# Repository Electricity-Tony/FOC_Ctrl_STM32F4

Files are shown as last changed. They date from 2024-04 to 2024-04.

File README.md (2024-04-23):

# FOC_Ctrl_STM32F4

* 基于 stm32F405rgt6 开发的 FOC 中大功率开发板

## 1 PCB设计文件

* stm32F405RGT6 minisystem

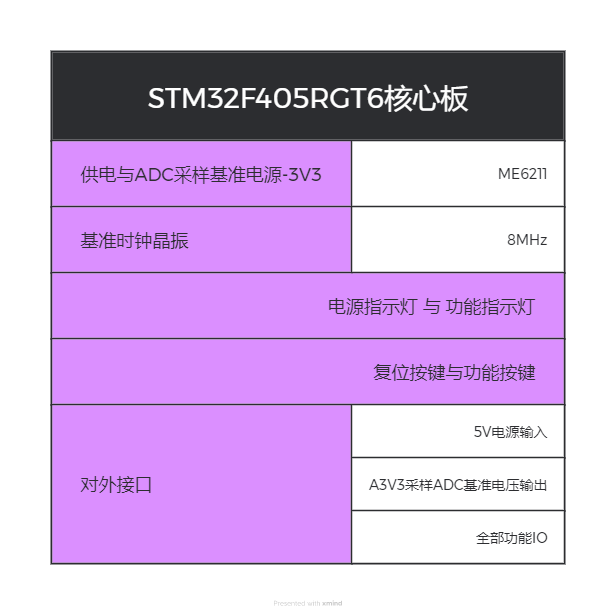
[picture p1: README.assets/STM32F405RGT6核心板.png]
STM32F405RGT6核心板


* power_board

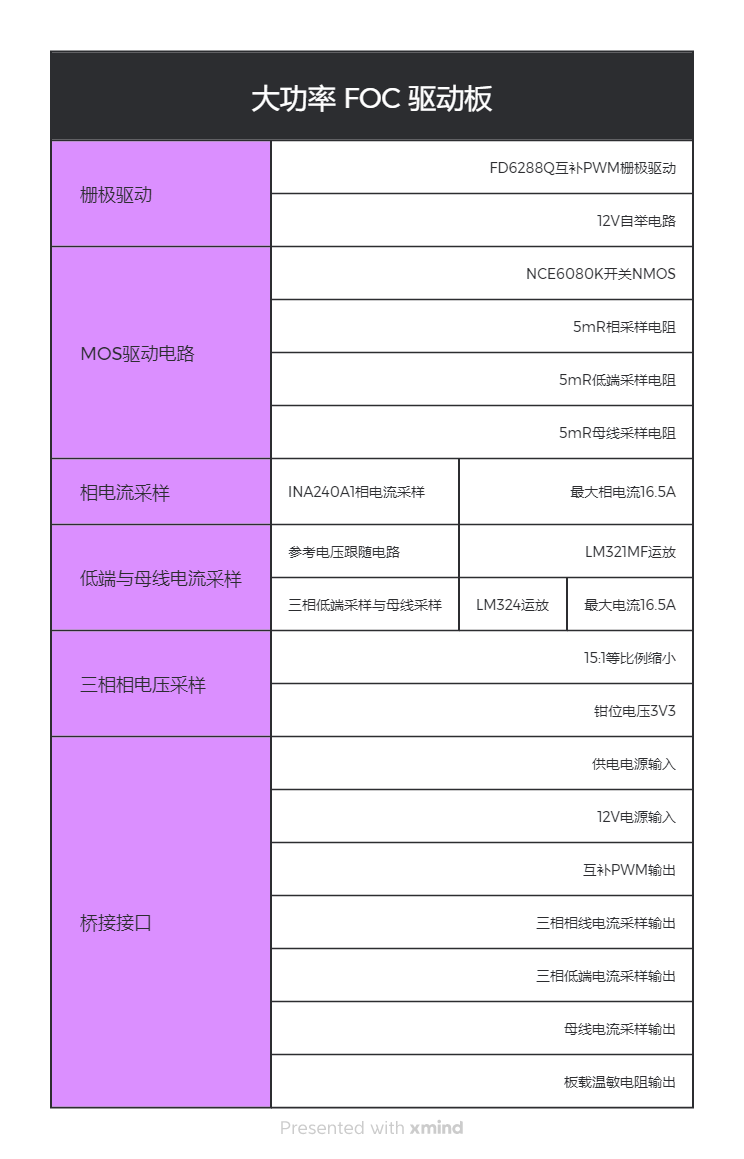
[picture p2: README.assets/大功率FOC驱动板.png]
大功率 FOC 驱动板


* base_board

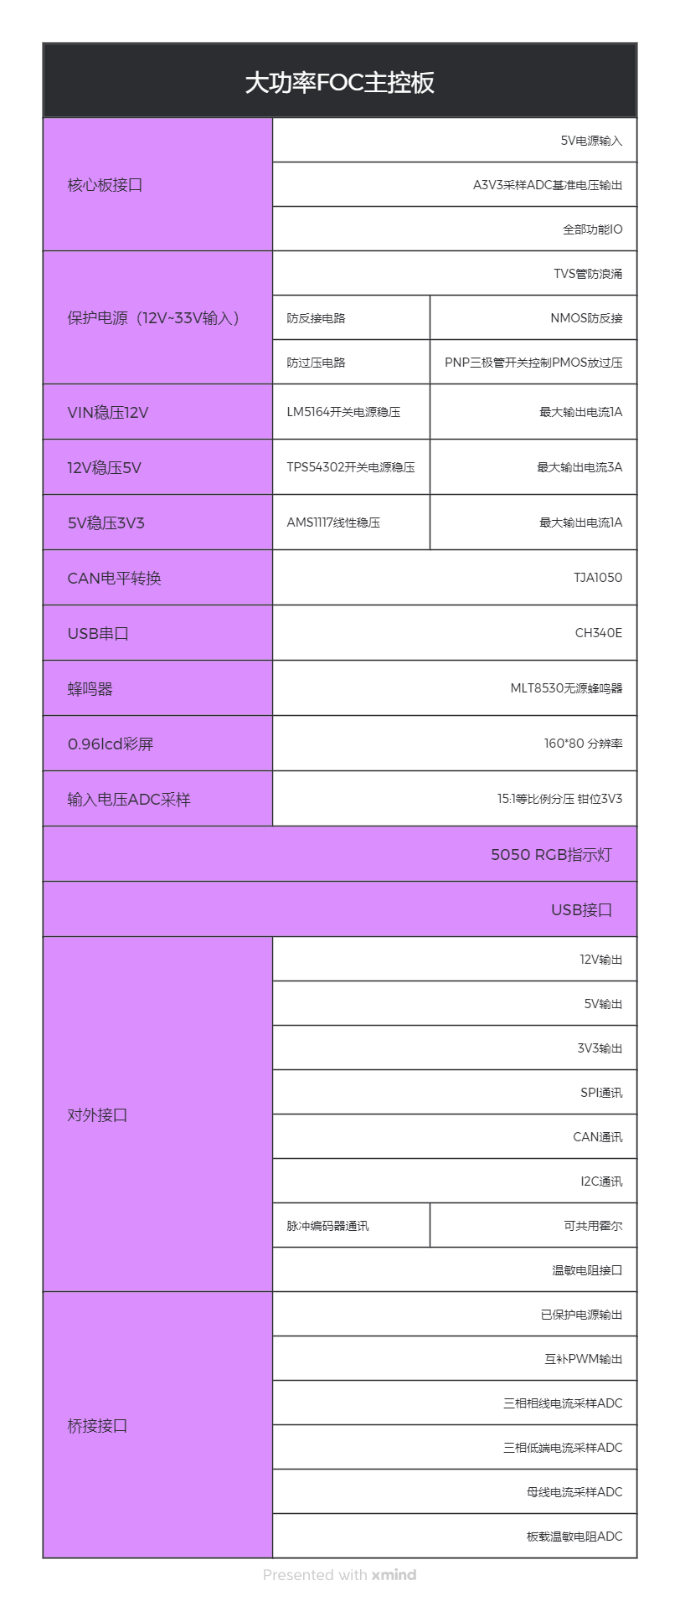
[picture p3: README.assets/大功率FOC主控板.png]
大功率FOC主控板


### 1 控制板设计文件

#### 1.1 输入电路设计

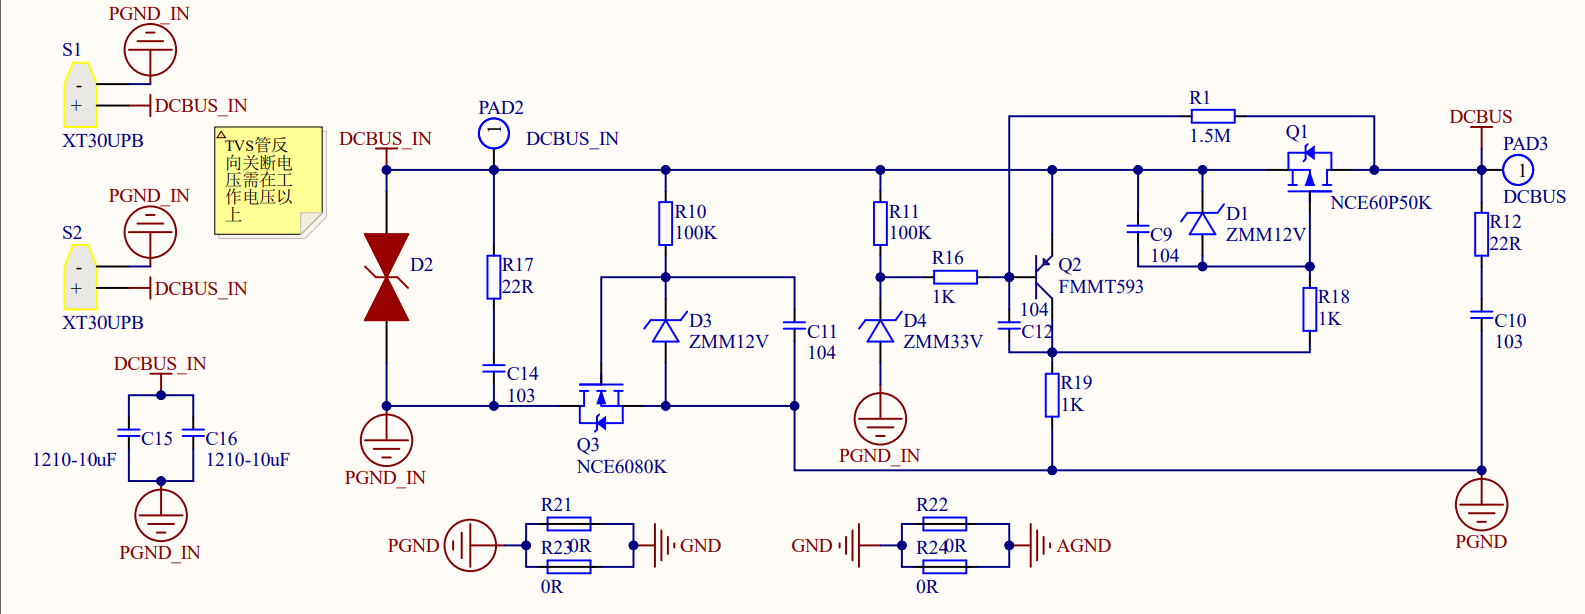
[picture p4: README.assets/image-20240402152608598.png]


* NCE6080K nmos 实现电源防反接
* NCE60P50K pmos 通过三极管及稳压管实现防过压
* RC 电路实现环启动
* TVS 管浪涌保护

> 实测反接保护与过压保护均可实现

#### 1.2 稳压电路设计

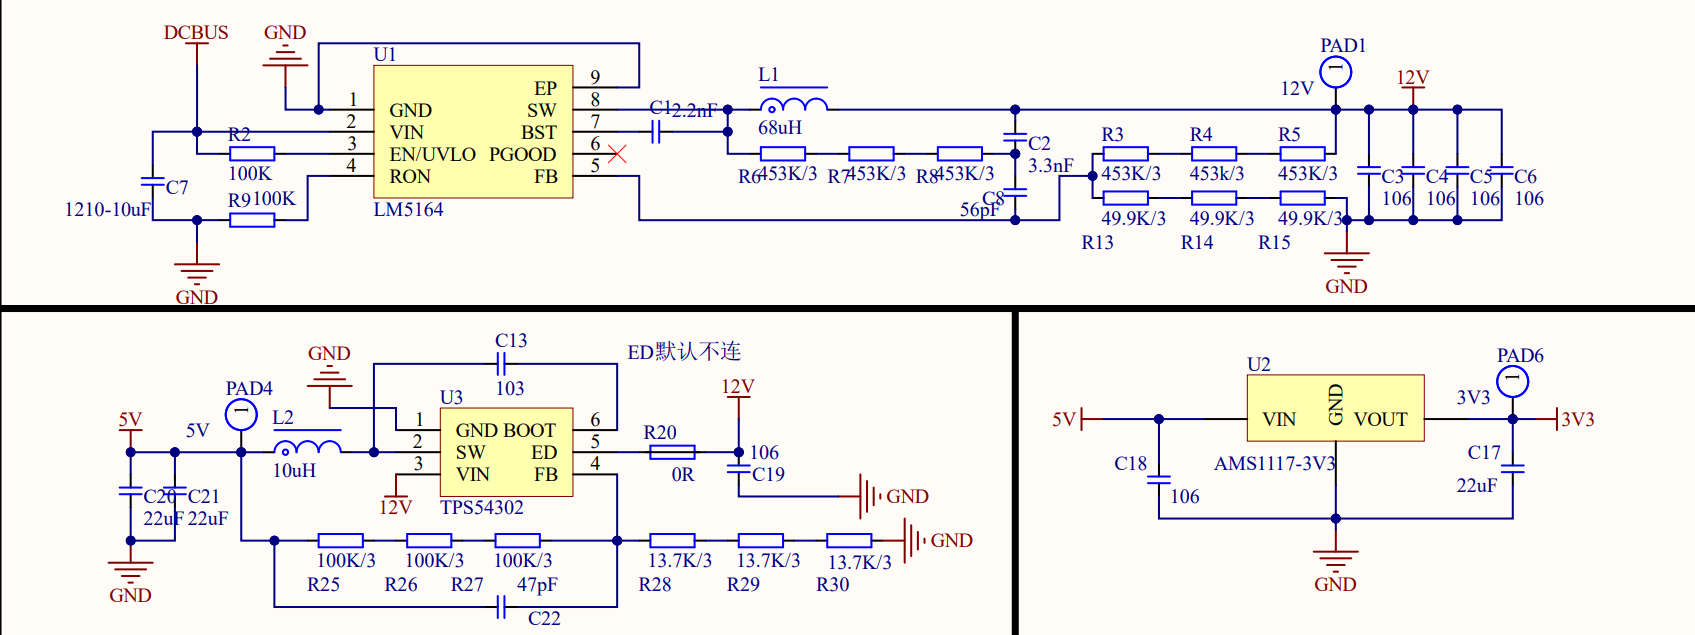
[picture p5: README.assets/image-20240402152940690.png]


* LM5164 宽幅电压输入 ，稳压12V，最大电流1A
* TP54302 稳压5V
* AMS1117 LDO稳压3V3

> LM5164 中 C1 = 2.2nF  必须要焊接，才能正常输出，3.3nF与56pF用于减少输出纹波，具体选择大小见datasheet
>
> 输出电压计算：$R_{FB2} = \frac{1.2V}{V_{OUT}-1.2V} \cdot R_{FB1}$
>
> 其余参数详见 datasheet

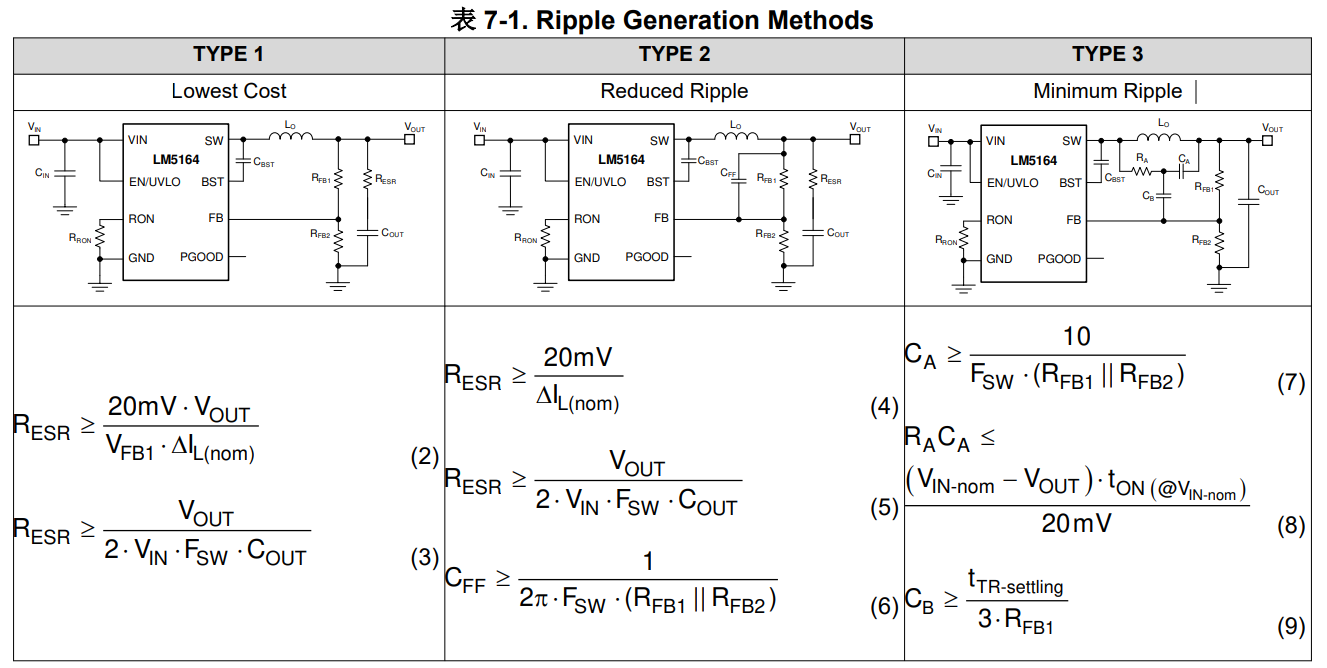
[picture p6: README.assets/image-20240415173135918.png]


> TPS54302 ED 角位欠压锁定角，内部上拉，当ED电压低于阈值电压实现欠压锁定，一般而言悬空即可使用，不使用欠压锁定功能
>
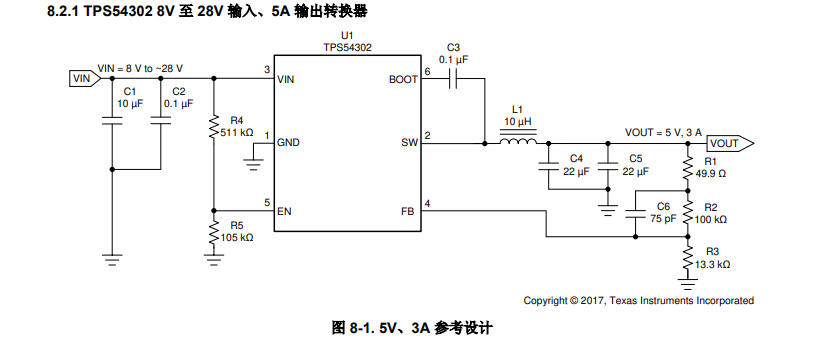
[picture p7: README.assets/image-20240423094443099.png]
> 
>
> 
>
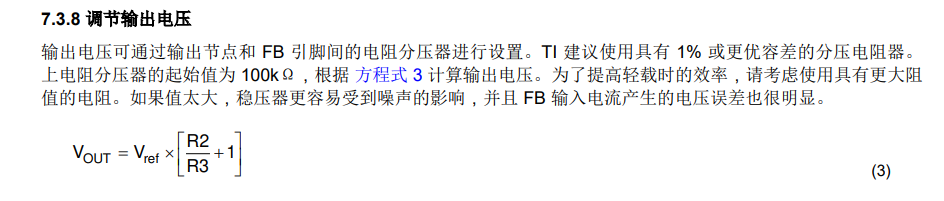
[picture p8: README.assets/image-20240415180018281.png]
> 输出电压计算：
>
> $V_{ref} = 0.596V$ , R2为分压上电阻，R3为分压下电阻

#### 1.3 外设设计

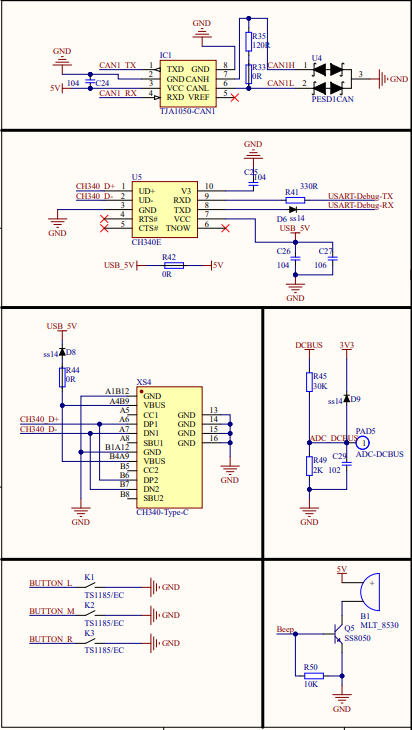
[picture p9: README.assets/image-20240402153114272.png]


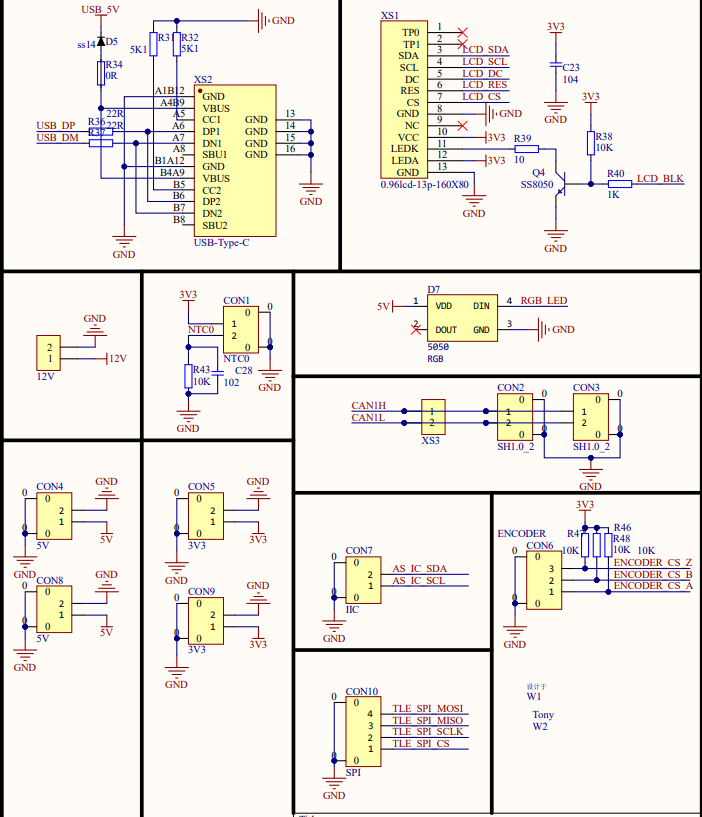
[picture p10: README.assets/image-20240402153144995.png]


* 预留外设 CAN，USART，USB，蜂鸣器，LCD屏幕，3个独立按键，各编码器通讯及供电接口

> CAN 中断电阻可通过是否焊接或短接 0R 电阻焊盘实现
>
> 5V 网络 与 USB5V 网络可通过 0R电阻 选择是否隔离，USB5V只提供给CH340串口芯片，避免主控反复上下电需要重新选择串口
>
> 串口 USB 的5V输入串接了一个二极管，纯在 0.7V 左右的压降，根据需要选择是否焊接

### 2 驱动板设计文件

#### 2.1 栅极驱动与自举电路

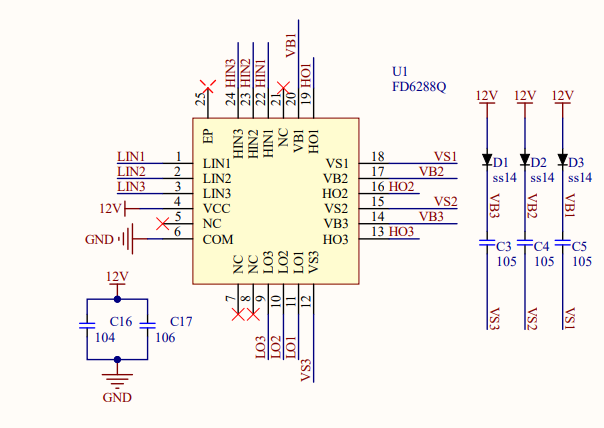
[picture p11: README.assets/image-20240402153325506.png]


* FD6288Q 栅极驱动，自带50ns死区保护，自举12V电路

#### 2.2 逆变电路

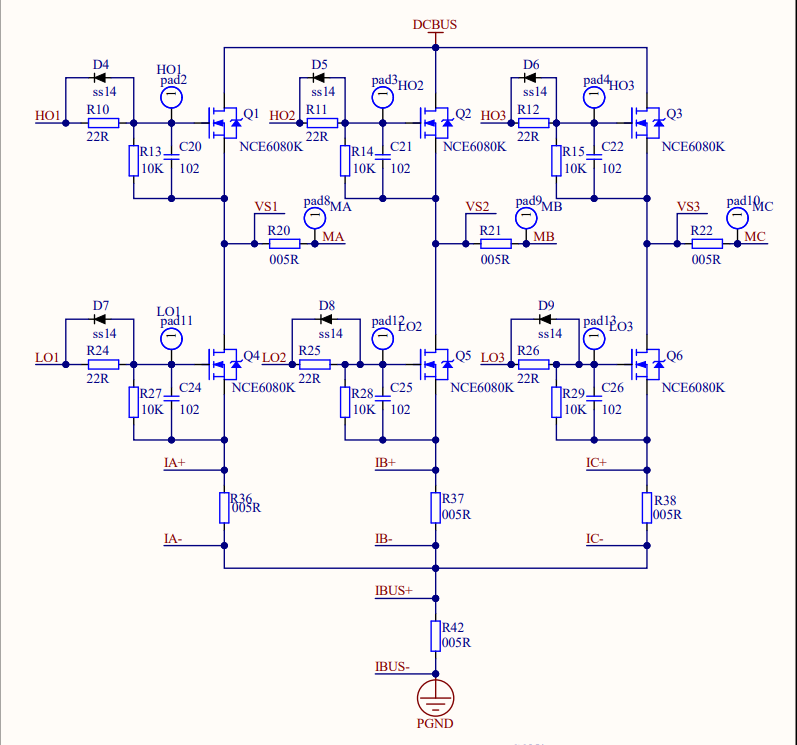
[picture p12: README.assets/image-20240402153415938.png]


* NCE6080K nmos 搭建逆变电路
* 各相线可通过 INA240 相线电流采样
* 三低端可通过 运放电流采用
* 母线电流采样

#### 2.3 电流采样运放电路

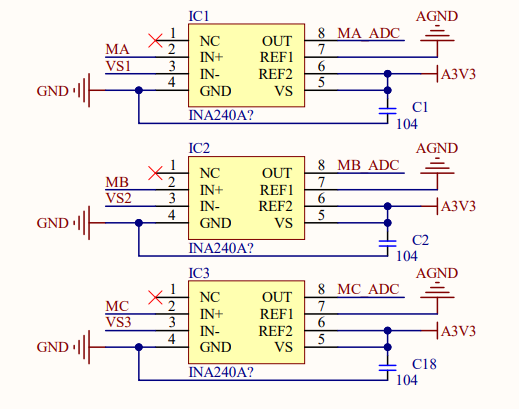
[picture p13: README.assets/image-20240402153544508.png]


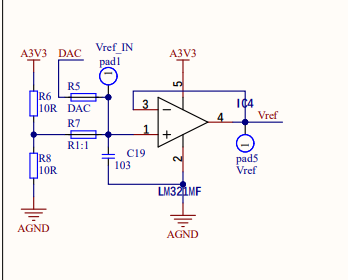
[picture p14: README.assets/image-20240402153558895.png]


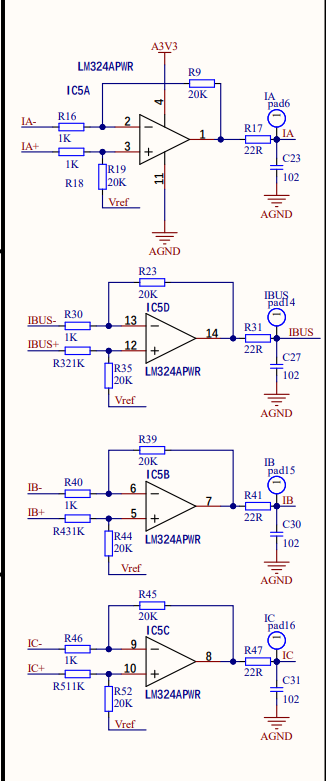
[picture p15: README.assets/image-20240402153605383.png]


* 相线通过 INA240 采样电阻设计 5mR，可自由选择A1和A2放大倍数确定采样电流大小
* LM321MF 运放实现参考电压电压跟随
* LM324APWR 4通道运放实现母线及低端采样

## 2 软件设计

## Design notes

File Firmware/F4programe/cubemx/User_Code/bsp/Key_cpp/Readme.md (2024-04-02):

# Key库使用教程

## 1 日志

 * @外设相关：<font color=Red>Key</font >

   @版本：<font color=Red>1.3</font >

   @维护：<font color=Red>Tony_Wang</font >

   @代码规范：<font color=Red>暂无</font>

   | 版本                               |                             功能                             |
   | :--------------------------------- | :----------------------------------------------------------: |
   | <font color=DeepSkyBlue>1.0</font> |    <font color=DeepSkyBlue>基本Cube配置与基本设置</font>     |
   | <font color=DeepSkyBlue>1.1</font> | <font color=DeepSkyBlue>重构为C++库，派生各类Key，并可用系统时钟调用长按</font> |
   | <font color=DeepSkyBlue>1.2</font> | <font color=DeepSkyBlue>Button长按修改为不松开仍然生效</font> |
   | <font color=DeepSkyBlue>1.3</font> | <font color=DeepSkyBlue>Button.update 修改为带返回值函数，返回值为状态，该准太会返回处于长按中的长按生效状态，此时，长按类的状态不更新</font> |

 ## 2 文件介绍

> | bsp_Key.cpp     | 按键主文件     |
> | --------------- | -------------- |
> | **bsp_Key.hpp** | **按键头文件** |

 ## 3 重要函数介绍

### 3.1 基类 Key

#### 3.1.1 Key结构大纲

```c++
/*****			自锁类按键构造函数				******/
class Key
{
	public:
		GPIO_TypeDef* GPIO_Port;	//按键结构体端口号
		uint16_t Pin;				//按键结构体引脚号
    
   		uint8_t State;			//实时当时的按键按下情况
    
		//成员函数
		Key(void){};
		Key(GPIO_TypeDef* GPIO_Port, uint16_t Pin);	
		void read(void);
	protected:
};
```

* 对每一个按键进行设置构造，内置IO端口和引脚号，可直接使用构造函数构造
* 设定为可以自锁类开关，只有按下与没按下两种状态

#### 3.1.2 按键当前值获取

```c++
void Key::read()
```

* 直接更新当前按键当前状态值

### 3.2 派生类Button

```c++
/*****			派生类按键构造函数				******/
class Button:public Key
{
	public:
		uint16_t time_check;			//长按时间判断域
		uint8_t Button_State;				//实际需要调用的状态	
		//成员函数
		Button(GPIO_TypeDef* GPIO_Port, uint16_t Pin,uint16_t time_check);
		void update(void);
	protected:	
	private:
		//运算储存区
		uint32_t time_flag;		//长按判断标志位
		uint8_t Ture_State;		//按键表示的状况标致,用于长按时间段内标致判断,目前仅由未使用内置时钟使用
		uint8_t Last_State;		//上一次检测状态
};
```

* 设定为不可自锁类按键开关，出现短按反转状态与长按 共三种状态

#### 3.2.3 逻辑可用状态值更新

```c++
Button_State Button::update()
```

* 对按键可用值进行更新，存放在State中
* 长按检测函数使用的是内置 systick 时钟，单位ms

 ## 4 自定义修改参数

 ## 5 基本使用方法

### 5.1 默认使用方法

* Cube配置中在<font color='DeepSkyBlue'>GPIO_INPUT</font>，设置为上拉。pull_up
* 设置用户自定义名称
* 声明需要的按键结构体并进行初始赋值
* 循环调用<font color='DeepSkyBlue'>Key.read() 或 Button.update</font>
* 需要对逻辑值进行判断时调用变量的<font color='DeepSkyBlue'>State 或 OUT_State</font>
* x = USER_Button.update(); x在长按持续期间会输出长按时候已经成立的状态，两倍长按时间后x变回 OUT_State 状态。用于交互中显示长按已经生效

 ## 6 其他注意

 t

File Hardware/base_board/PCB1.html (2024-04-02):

Altium customize

# Board Information Report

Date: | | 2024/1/30
Time: | | 20:15:17
Elapsed Time: | | 00:00:00
Filename: | | G:\BaiduSyncdisk\Synchronization\Tony diy\Core_FOC_F4_Ctrl\base_board\PCB1.PcbDoc
Units: | | mmmils

## Contents

Contents

Routing

Routing Information

Other

Net Track Width

## Routing

Routing Information
Routing completion | 100.00%
Connections | 330
Connections routed | 330
Connections remaining | 0

Back to top

## Other

Net Track Width | Count
4mils | 105
Total | 105

Back to top

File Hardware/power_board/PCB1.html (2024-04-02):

Altium customize

# Board Information Report

Date: | | 2024/2/8
Time: | | 18:05:59
Elapsed Time: | | 00:00:00
Filename: | | G:\BaiduSyncdisk\Synchronization\Tony diy\Core_FOC_F4_Ctrl\power_board\PCB1.PcbDoc
Units: | | mmmils

## Contents

Contents

Routing

Routing Information

Other

Net Track Width

## Routing

Routing Information
Routing completion | 100.00%
Connections | 310
Connections routed | 310
Connections remaining | 0

Back to top

## Other

Net Track Width | Count
4mils | 67
Total | 67

Back to top

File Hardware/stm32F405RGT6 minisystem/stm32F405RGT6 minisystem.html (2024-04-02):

Altium customize

# Board Information Report

Date: | | 2023/12/20
Time: | | 17:34:09
Elapsed Time: | | 00:00:00
Filename: | | G:\BaiduSyncdisk\Synchronization\Tony diy\stm32F405RGT6 minisystem\stm32F405RGT6 minisystem.PcbDoc
Units: | | mmmils

## Contents

Contents

Routing

Routing Information

Other

Net Track Width

## Routing

Routing Information
Routing completion | 100.00%
Connections | 126
Connections routed | 126
Connections remaining | 0

Back to top

## Other

Net Track Width | Count
6mils | 63
Total | 63

Back to top

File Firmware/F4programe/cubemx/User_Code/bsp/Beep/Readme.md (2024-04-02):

# RM2020电控 Board Support Package

## 综述

> 本BSP库根据个人调试和对RM2019代码工程阅读来构建,难免有疏漏之处,目前虽无运行上的BUG,但希望在使用本BSP库过程中出现任何BUG及时提出,以便修正

* @外设相关：<font color=Red>Beep</font> 

  @版本：<font color=Red>1.0</font> 

  @维护：<font color=Red>Evan-GH</font> 

  @代码规范：<font color=Red>RM电控代码规范</font>

  | 版本                               |                             功能                             |
  | :--------------------------------- | :----------------------------------------------------------: |
  | <font color=DeepSkyBlue>1.0</font> | <font color=DeepSkyBlue>根据代码规范修改上届代码库中的蜂鸣器库，整合乐谱</font> |
  
* 对外接口函数

```C
void bsp_beep_Music_Handle(void);//将这个函数放在定时器更新里面 周期根据歌曲特性来自行改变
void bsp_beep_Music_Play(bsp_beep_Song* head);	//开始演奏某个歌曲
void bsp_beep_Music_Stop(void); //音乐停止
```

> 当你需要演奏某个歌曲的时候，调用演奏函数，需要停止的时候调用停止函数，Handle函数放在某个周期函数里面更新。

* 对外结构体和变量

```C
typedef struct  song
{
	unsigned short int a; //代表音符
	unsigned char p;      //代表音符节拍
}bsp_beep_Song;
//歌曲结构体 记得加结束符 格式为{对应音，该音是什么音符}

//对外变量为具体乐谱
extern bsp_beep_Song warning[];
extern bsp_beep_Song warning1_L[];
extern bsp_beep_Song warning2_L[];
extern bsp_beep_Song warning3_L[];
extern bsp_beep_Song warning4_L[];
extern bsp_beep_Song warning5_L[];
extern bsp_beep_Song warning6_L[];
extern bsp_beep_Song warning7_L[];
extern bsp_beep_Song warning8_L[];
extern bsp_beep_Song warning1_M[];
extern bsp_beep_Song warning2_M[];
extern bsp_beep_Song warning3_M[];
extern bsp_beep_Song warning4_M[];
extern bsp_beep_Song warning5_M[];
extern bsp_beep_Song warning6_M[];
extern bsp_beep_Song warning7_M[];
extern bsp_beep_Song warning8_M[];
extern bsp_beep_Song warning1_H[];
extern bsp_beep_Song warning2_H[];
extern bsp_beep_Song warning3_H[];
extern bsp_beep_Song warning4_H[];
extern bsp_beep_Song warning5_H[];
extern bsp_beep_Song warning6_H[];
extern bsp_beep_Song warning7_H[];
extern bsp_beep_Song warning8_H[];
extern bsp_beep_Song warningx[];
extern bsp_beep_Song jile[];		//极乐净土
extern bsp_beep_Song Castle_in_the_Sky[]; //天空之城
extern bsp_beep_Song ItsOK[];
extern bsp_beep_Song Little_star[]; //小星星
extern bsp_beep_Song INTEL[];		//英特尔经典音效
extern bsp_beep_Song Song_of_Joy[];
extern bsp_beep_Song Kontora[];		
extern bsp_beep_Song News[];		//新闻音效
extern bsp_beep_Song VOCALOID_1[]; 	//末世歌者
```

> 对外变量主要包含的是乐谱存储数组

## 使用方法

* 1.加载本bsp库到工程中

```C
#include "bsp_beep.h"
```

* 2.使用**void bsp_beep_Music_Play(bsp_beep_Song* head)** 函数演奏你想要演奏的音乐，比如极乐净土：

```C
bsp_beep_Music_Play(jile);
```

* 3.在某个周期执行的函数中放置更新函数：

```C
 while (1)
  {
    /* USER CODE END WHILE */
		bsp_beep_Music_Handle();	//音乐更新句柄
		HAL_Delay(50);						//延时，根据音乐效果自己更改
    /* USER CODE BEGIN 3 */
  }
  /* USER CODE END 3 */
```

> 对于音乐要求比较高的可以自行修改音乐持续时间，音调，音乐间隔时间来获得更好的体验，这里不再赘述。

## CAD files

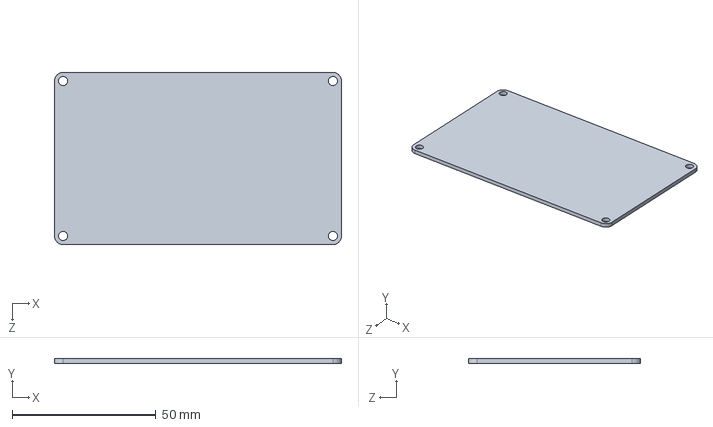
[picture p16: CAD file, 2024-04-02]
Hardware/base_board/sw/board.SLDPRT
100.0 x 1.60 x 60.0 mm

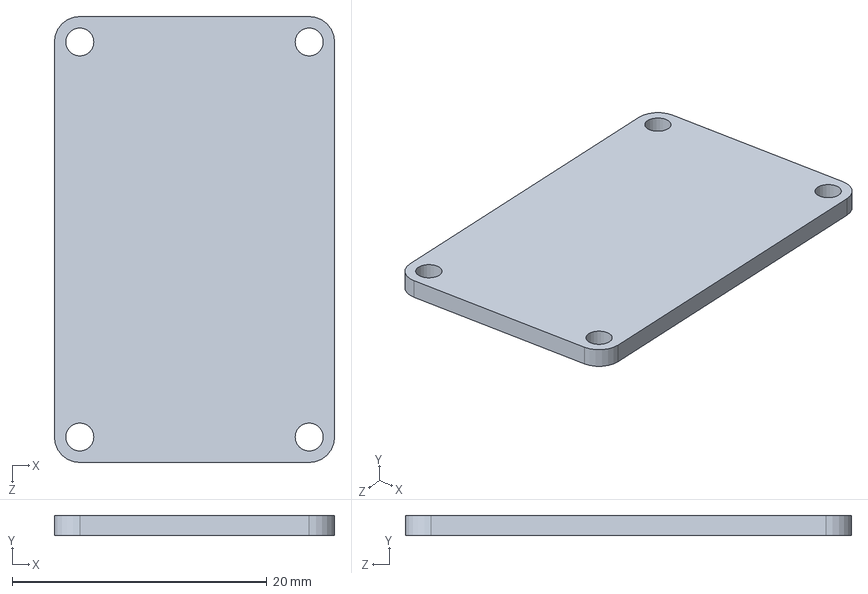
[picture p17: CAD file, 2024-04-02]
Hardware/stm32F405RGT6 minisystem/电路板.SLDPRT
22.0 x 1.60 x 35.0 mm

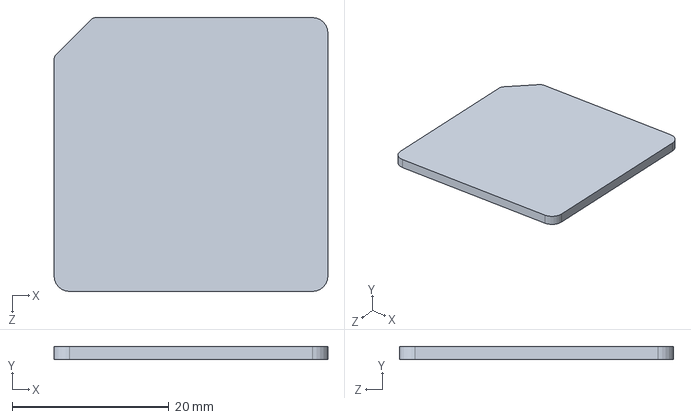
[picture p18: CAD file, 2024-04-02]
Hardware/stm32F405RGT6 minisystem/电路板图/电路板.SLDPRT
35.0 x 1.60 x 35.0 mm

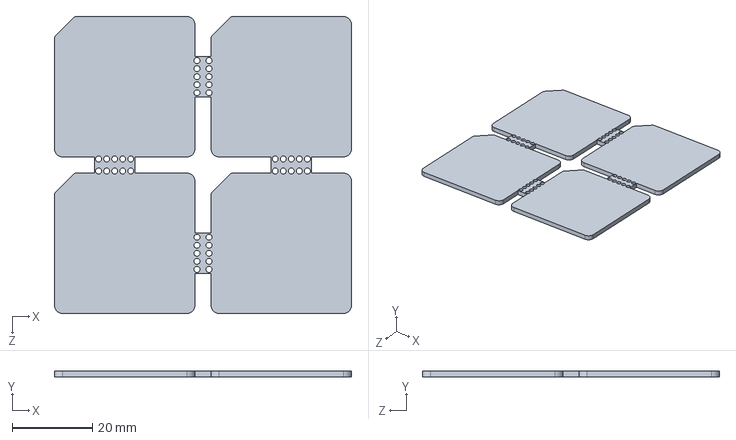
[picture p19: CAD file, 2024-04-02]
Hardware/stm32F405RGT6 minisystem/电路板图/组合板.SLDPRT
74.0 x 1.60 x 74.0 mm

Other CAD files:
Hardware/power_board/sw/board.SLDPRT
Hardware/base_board/sw/board.DXF
Hardware/power_board/sw/board.DXF
Hardware/stm32F405RGT6 minisystem/电路板.DXF
Hardware/stm32F405RGT6 minisystem/电路板图/电路板.DXF
Hardware/stm32F405RGT6 minisystem/电路板图/组合板.DXF

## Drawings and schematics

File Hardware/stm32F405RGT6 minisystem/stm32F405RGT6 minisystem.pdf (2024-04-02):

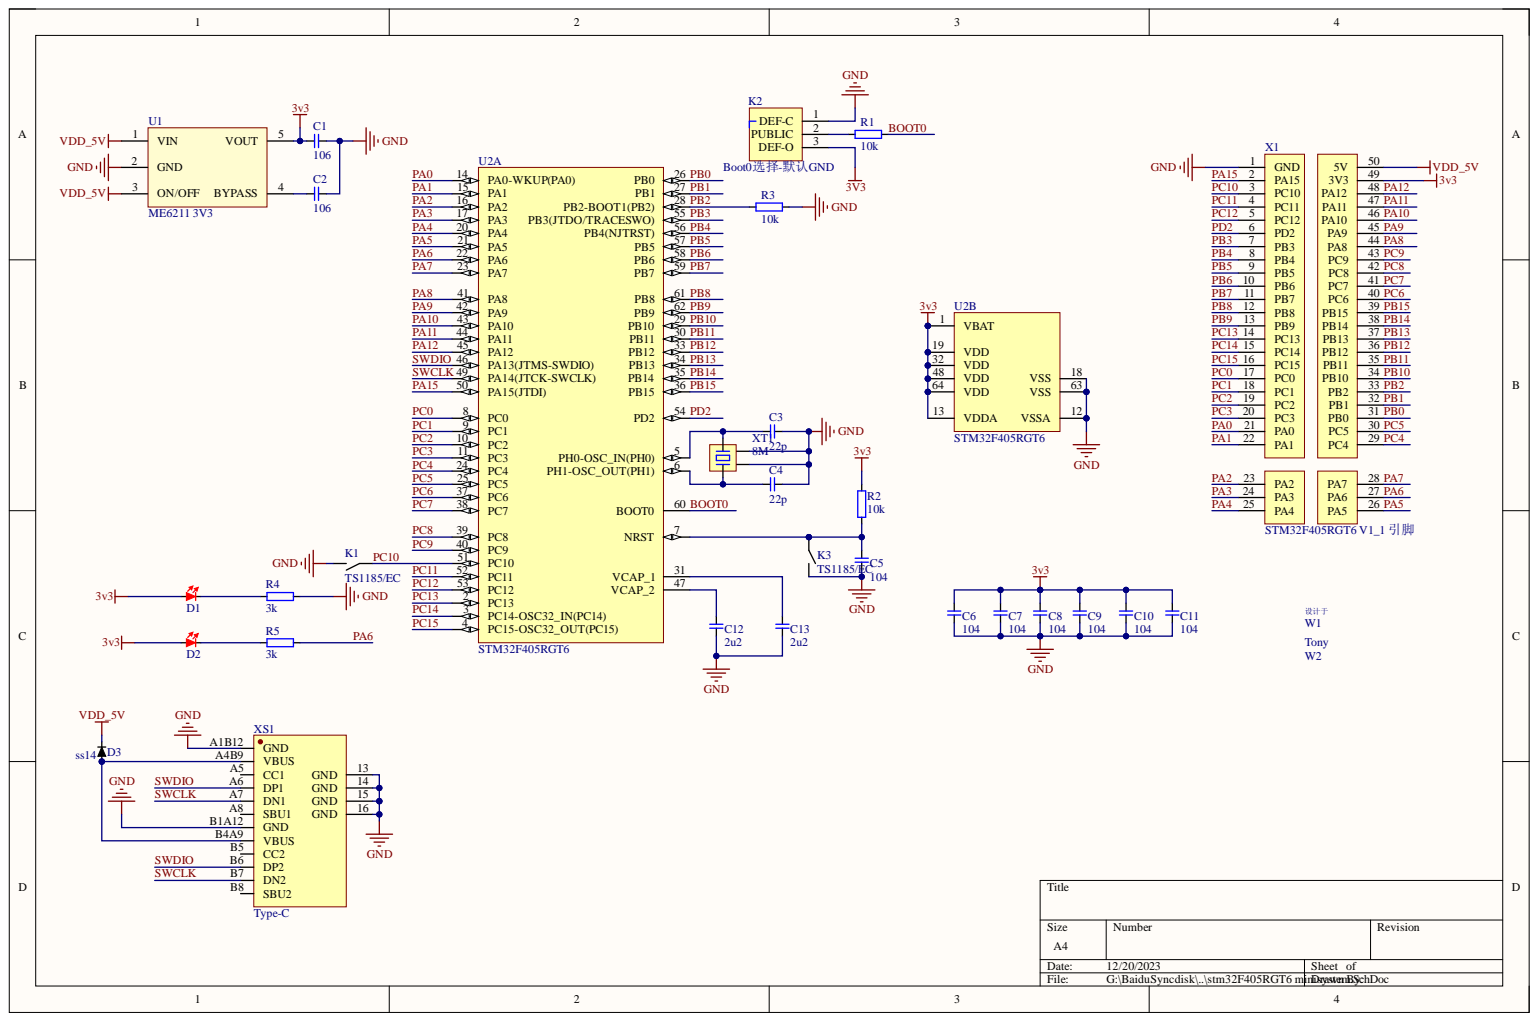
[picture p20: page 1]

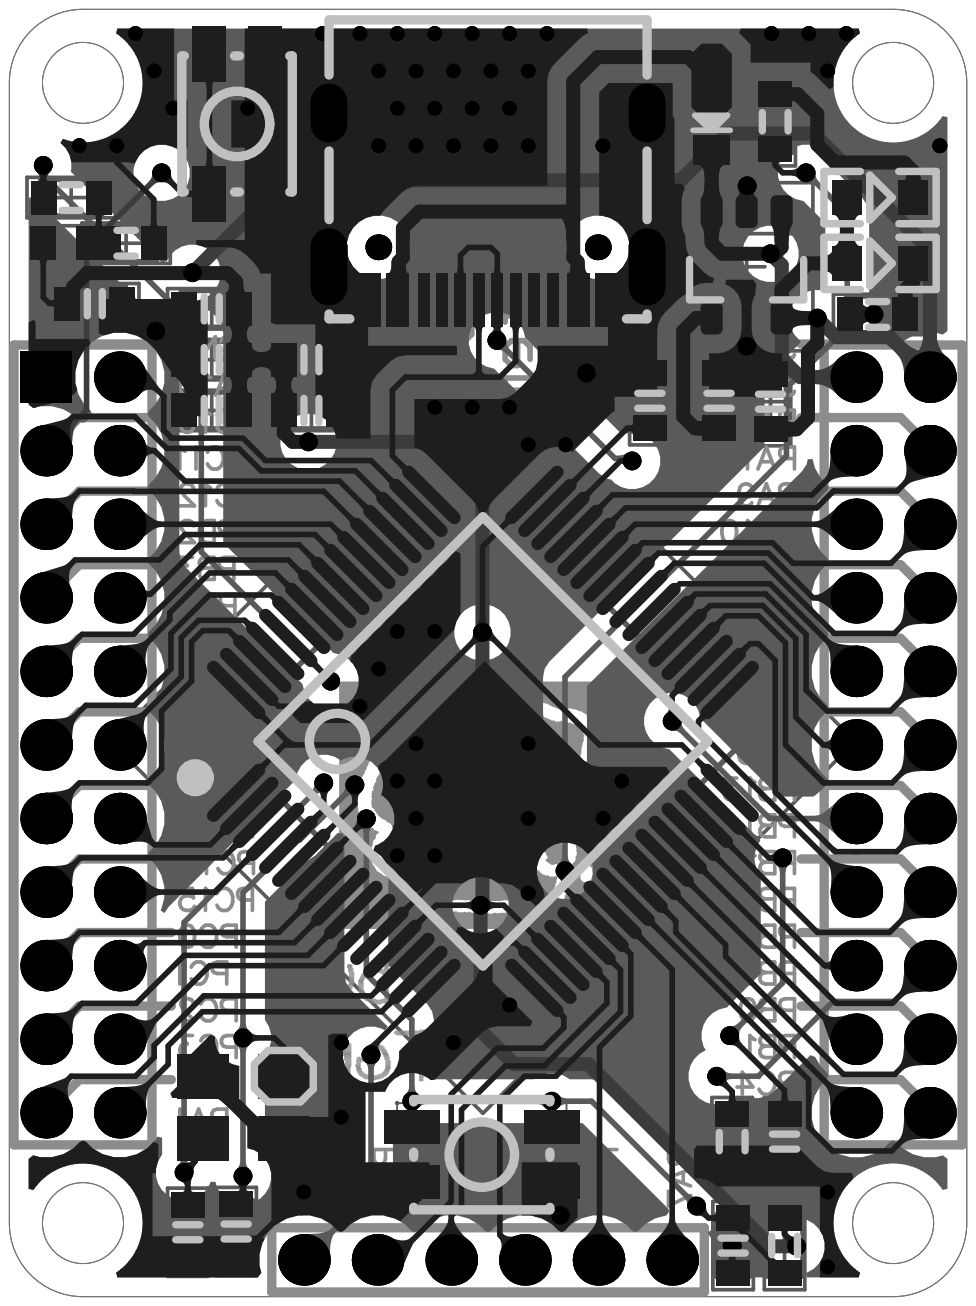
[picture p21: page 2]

Comment | Description | Designator | Footprint | LibRef | Quantity
106 | | C1, C2 | CAP_0603 | cap | 2
22p | | C3, C4 | CAP_0603 | cap | 2
104 | | C5, C6, C7, C8, C9, C10, C11 | CAP_0603 | cap | 7
2u2 | | C12, C13 | CAP_0603 | cap | 2
led | | D1, D2 | led0603 | led | 2
ss14 | | D3 | SOD-323 | Diode | 1
TS1185/EC | 3*4*2 立贴轻触开关 2Pin/4Pin | K1, K3 | TS-1185EC-X-X-X | Button-LT-3040 | 2
Boot0选择-默认 GND | 单刀双掷1-2 | K2 | Switch 1-2 0603 | Switch 1-2 | 1
10k | | R1, R2, R3 | RES_0603 | Res | 3
3k | | R4, R5 | RES_0603 | Res | 2
ME6211 3V3 | LDO | U1 | SOT23-5 | ME6211 | 1
STM32F405RGT6 | | U2 | LQFP64 | STM32F405RGT6 | 1
设计于 | | W1 | designed by（430-70） | 设计于 | 1
Tony | | W2 | Tony_2(200-70) | Tony | 1
STM32F405RGT6 V1_1 引脚 | | X1 | STM32F405RGT6 V1_1引脚 | STM32F405RGT6 V1_1 引脚 | 1
Type-C | | XS1 | TypeC-304-16BCP | Type-C母口 | 1
8M | | XT1 | SMD3225_4p | XTAL-4P | 1

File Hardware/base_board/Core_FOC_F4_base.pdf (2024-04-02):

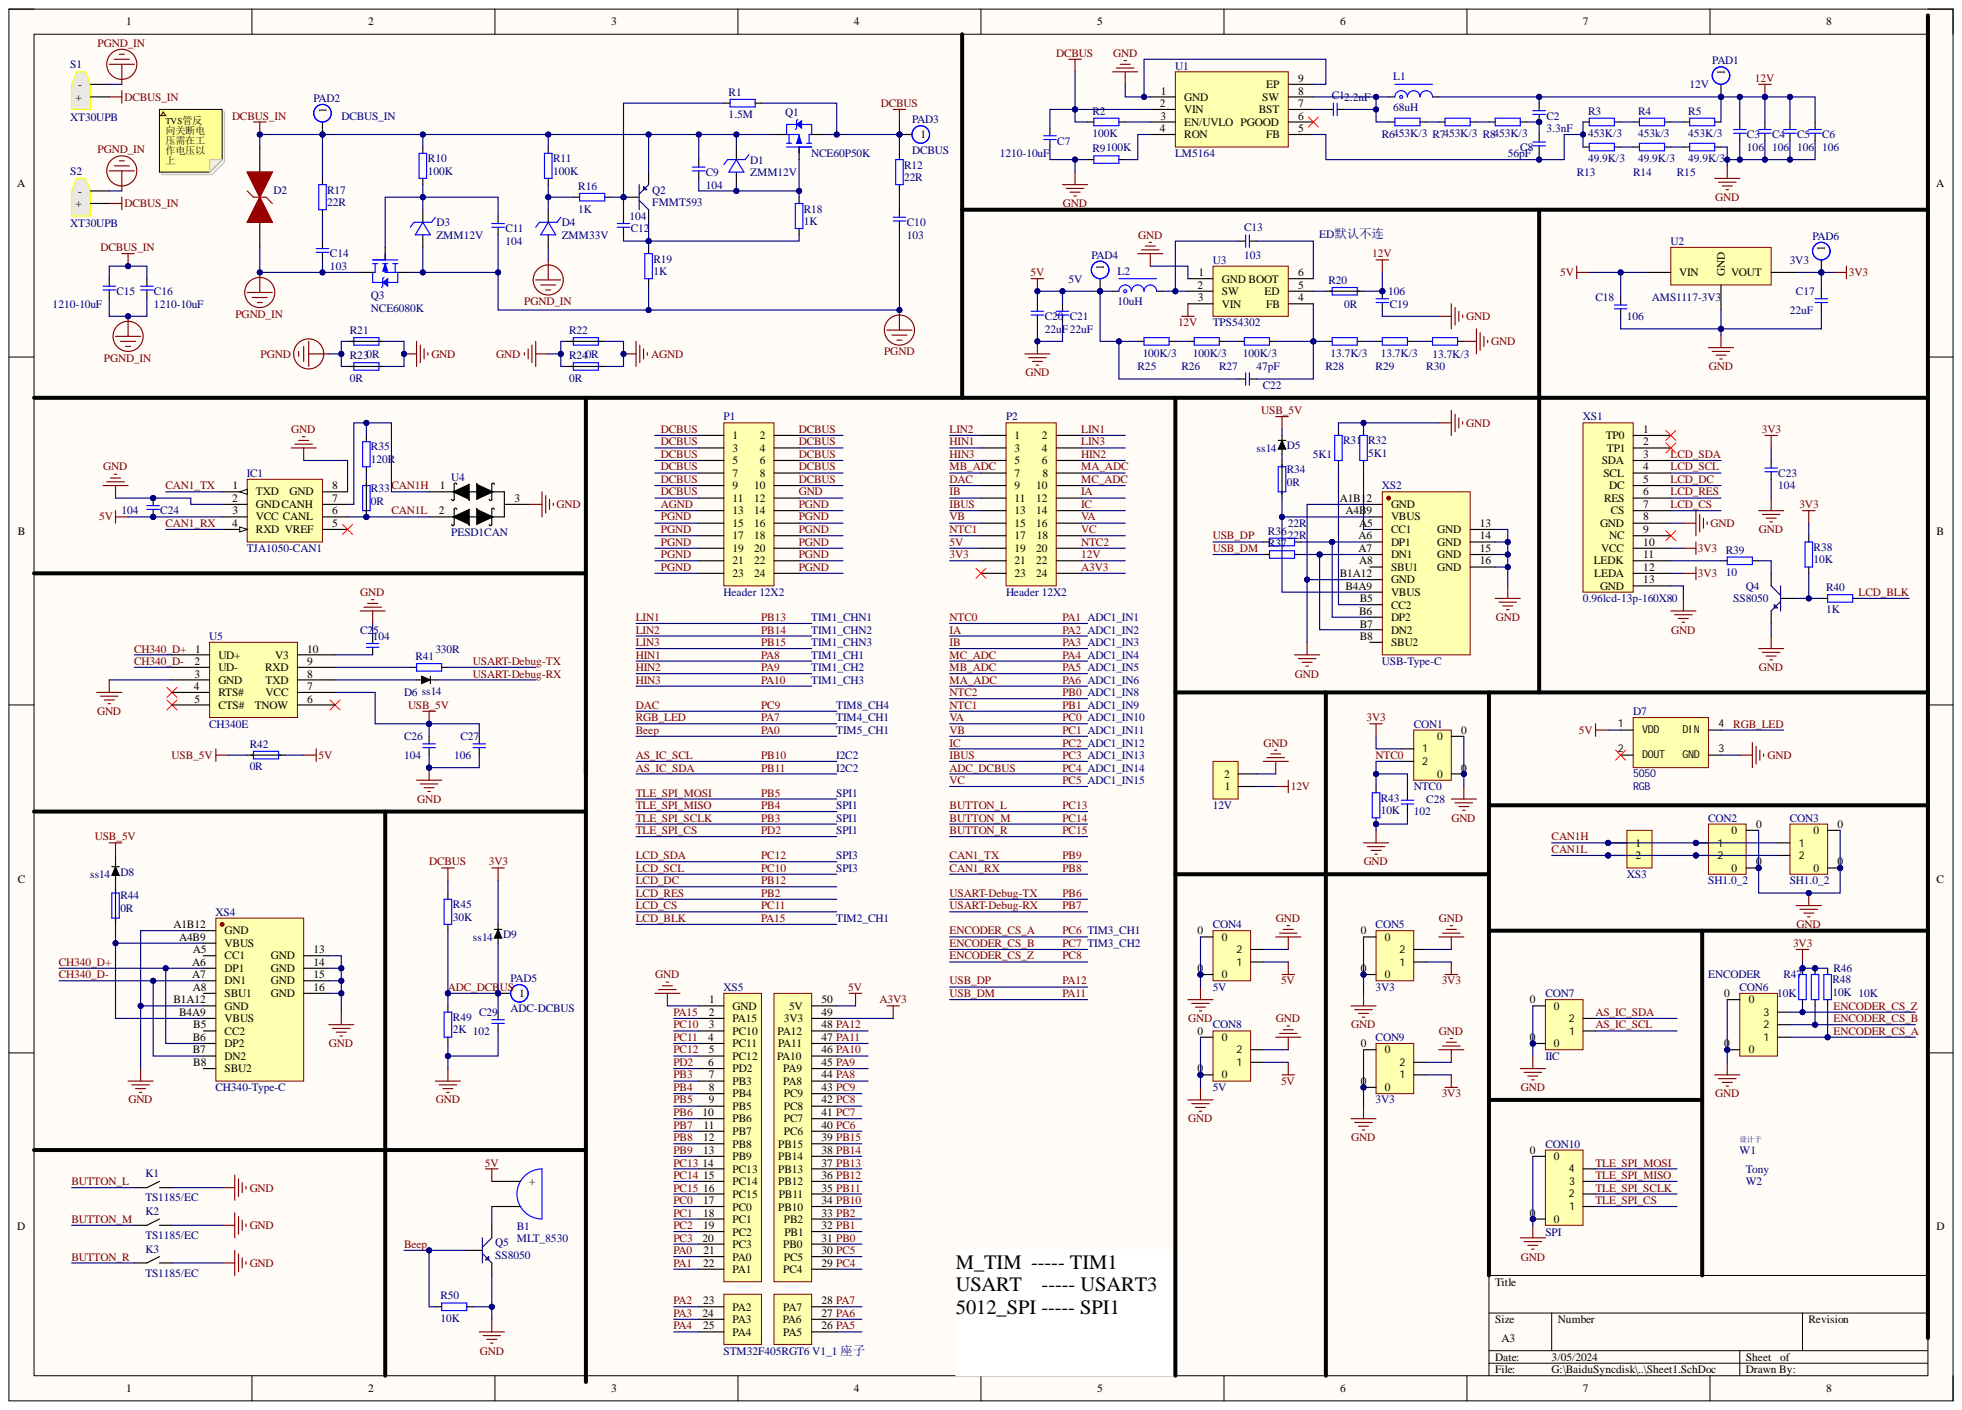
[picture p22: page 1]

VIN 2

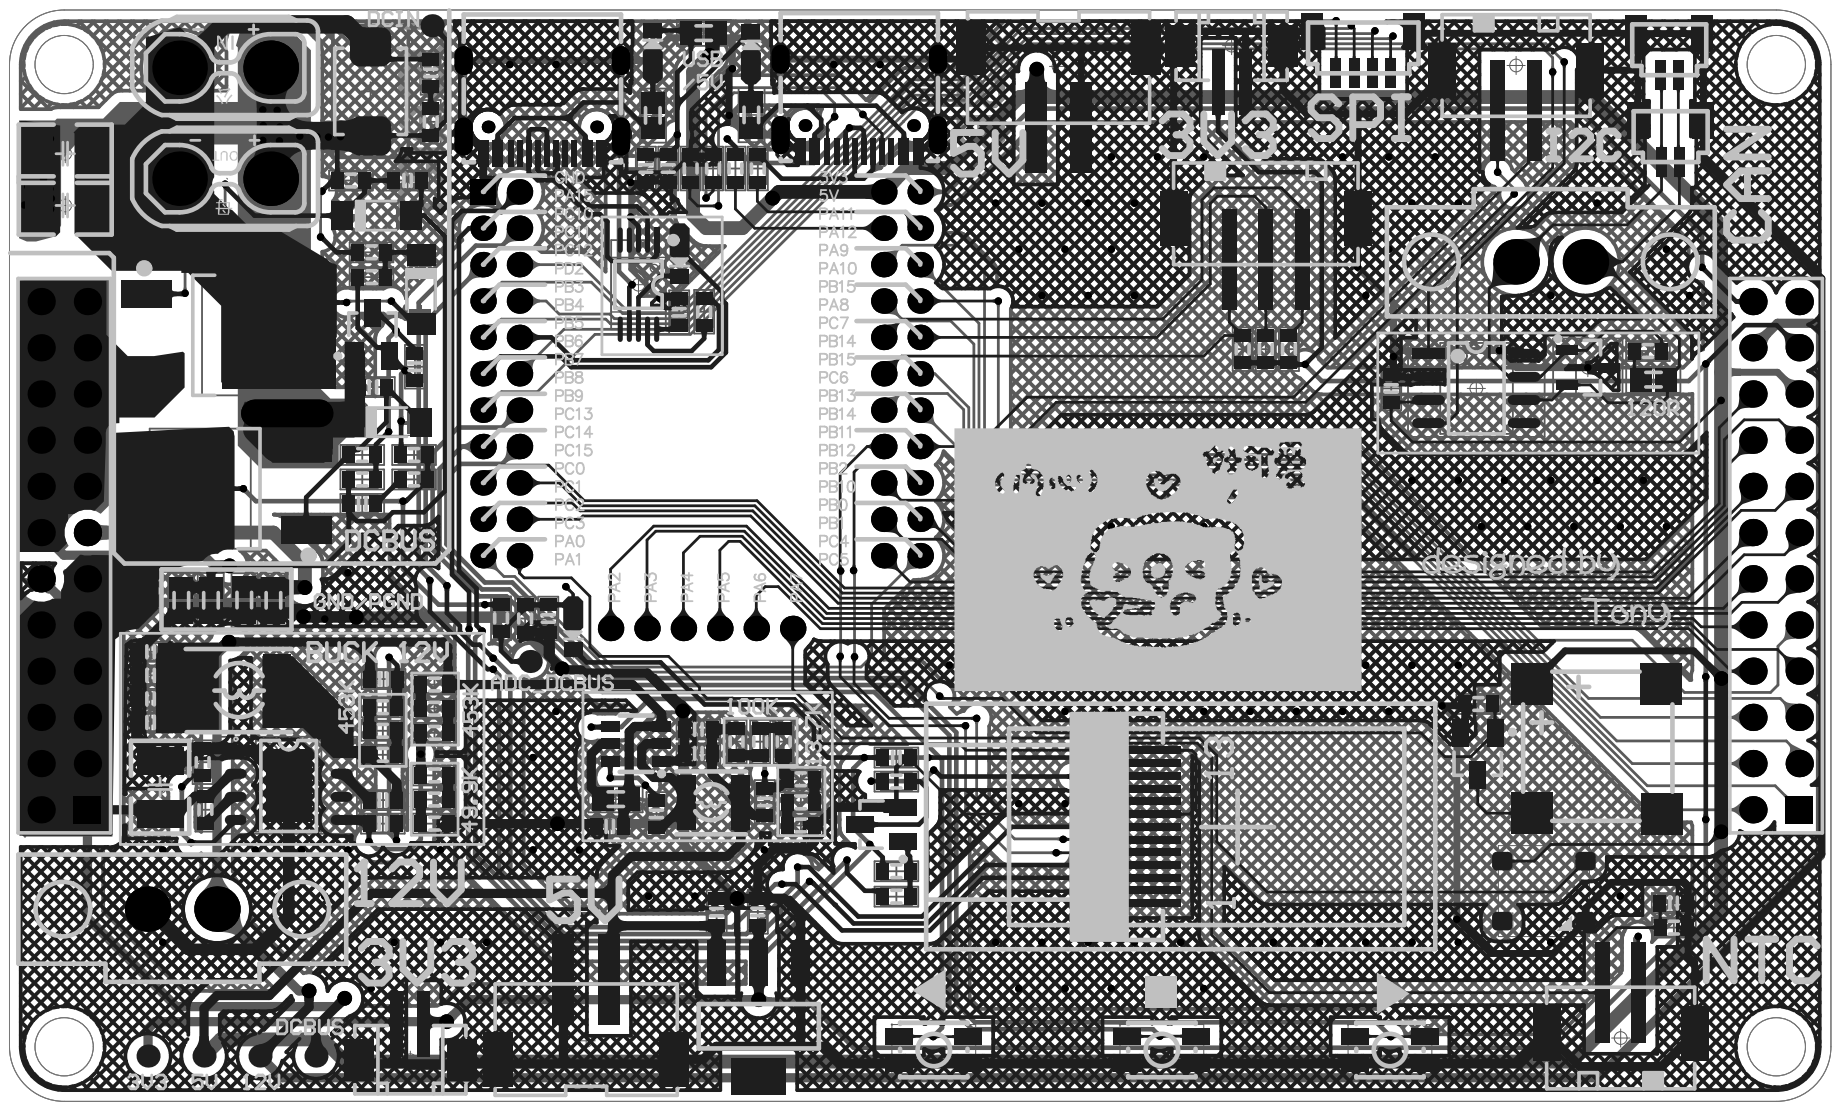
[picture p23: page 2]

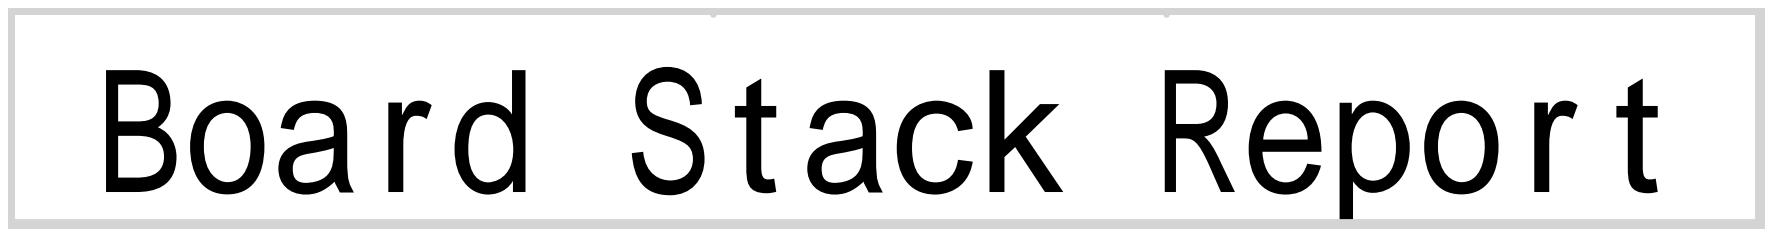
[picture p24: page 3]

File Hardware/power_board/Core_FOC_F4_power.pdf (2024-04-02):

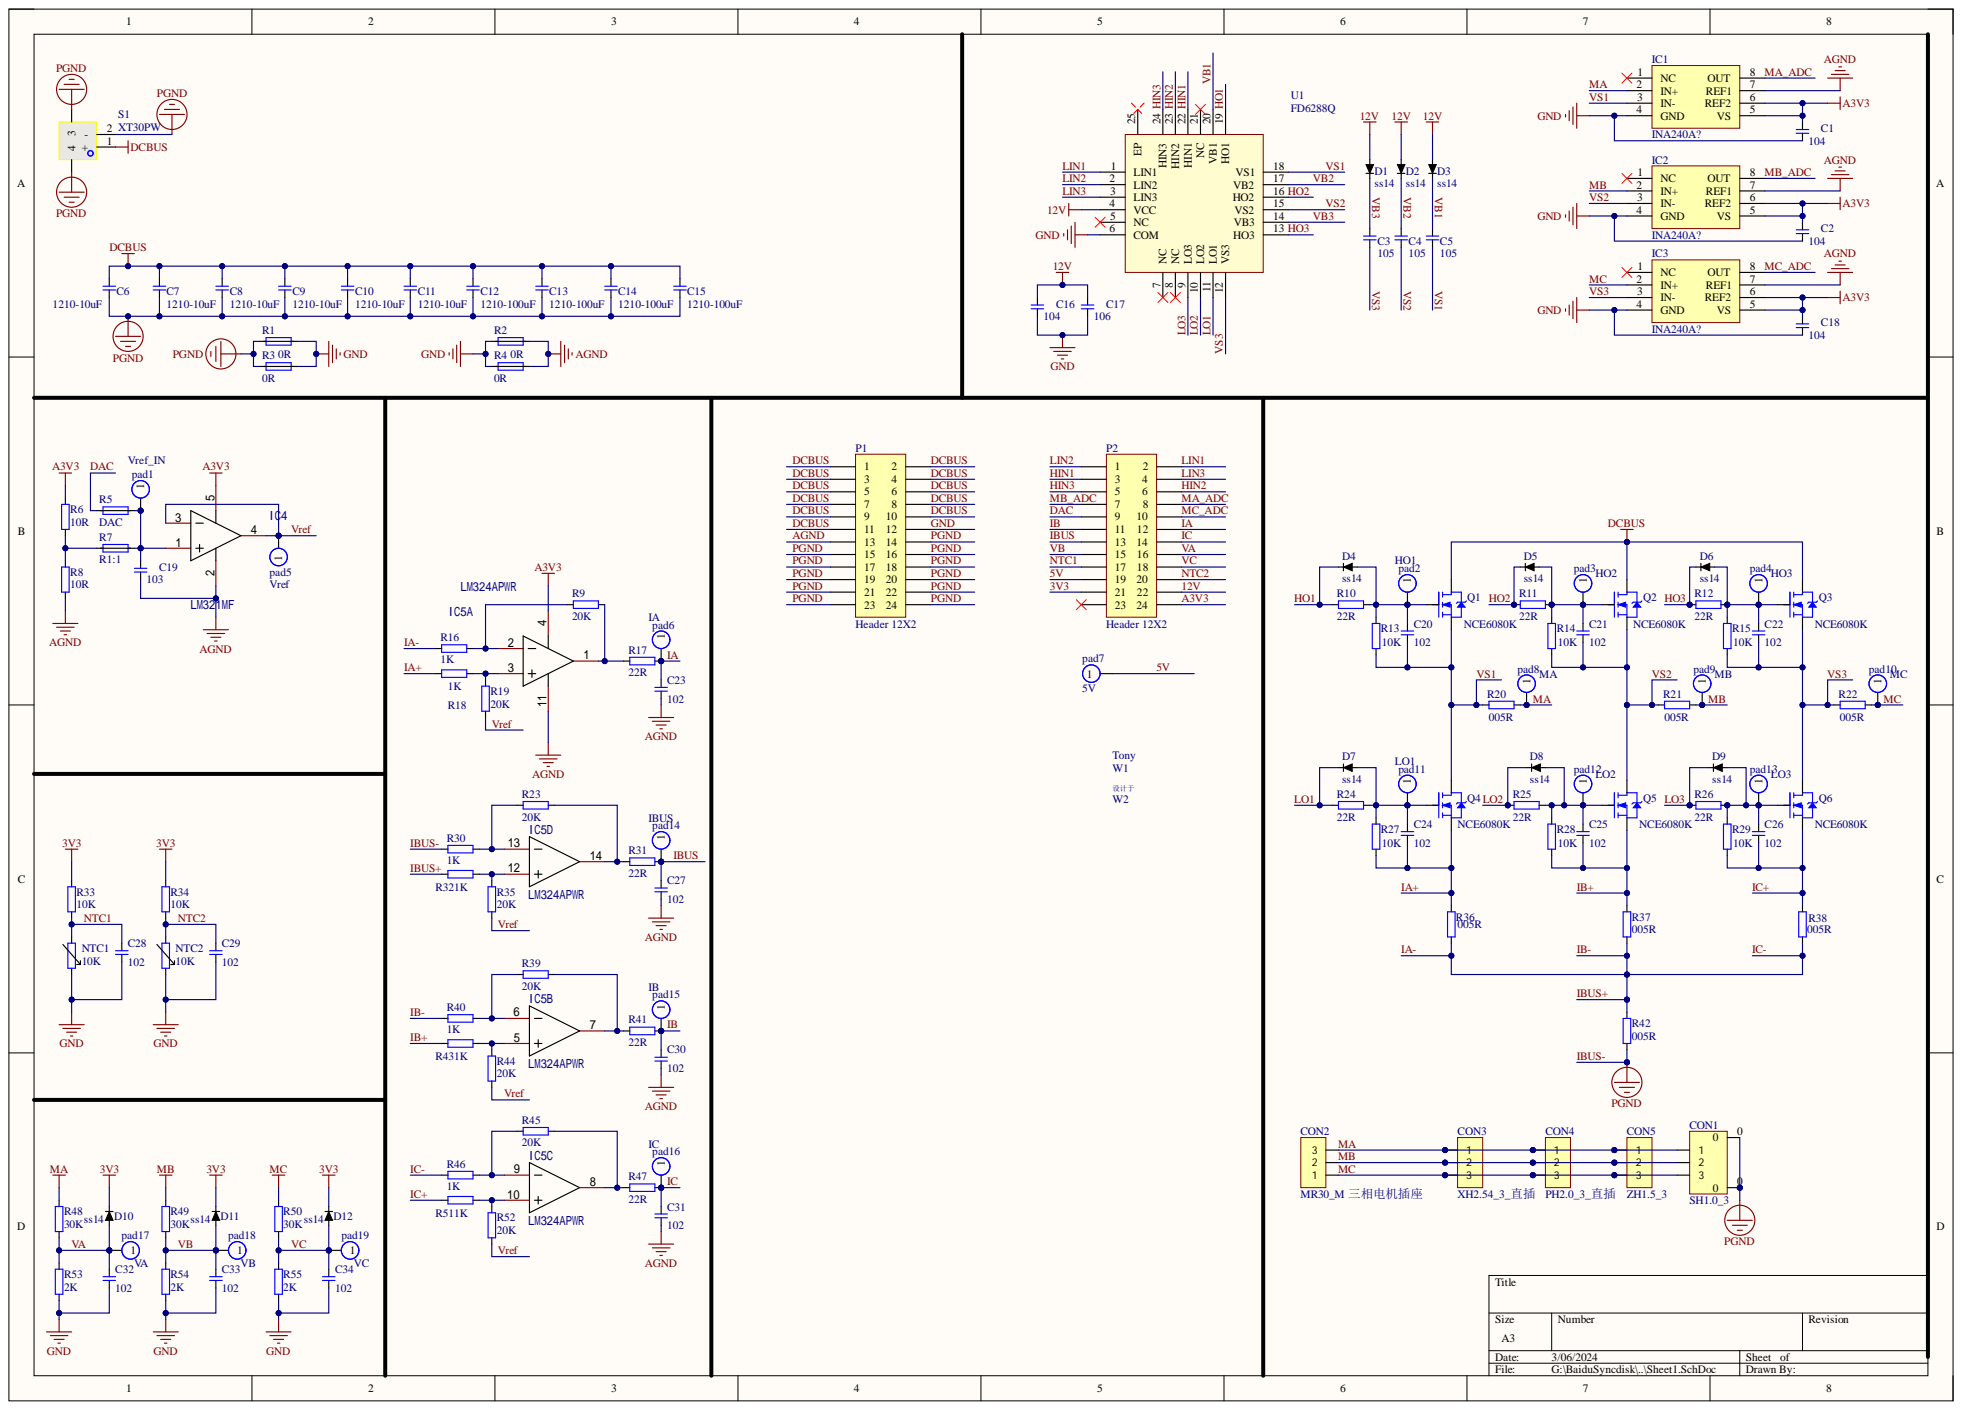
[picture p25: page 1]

R23
13 | 20K

MB | 2 | 2 | 2
MC | 3 | 3 | 3

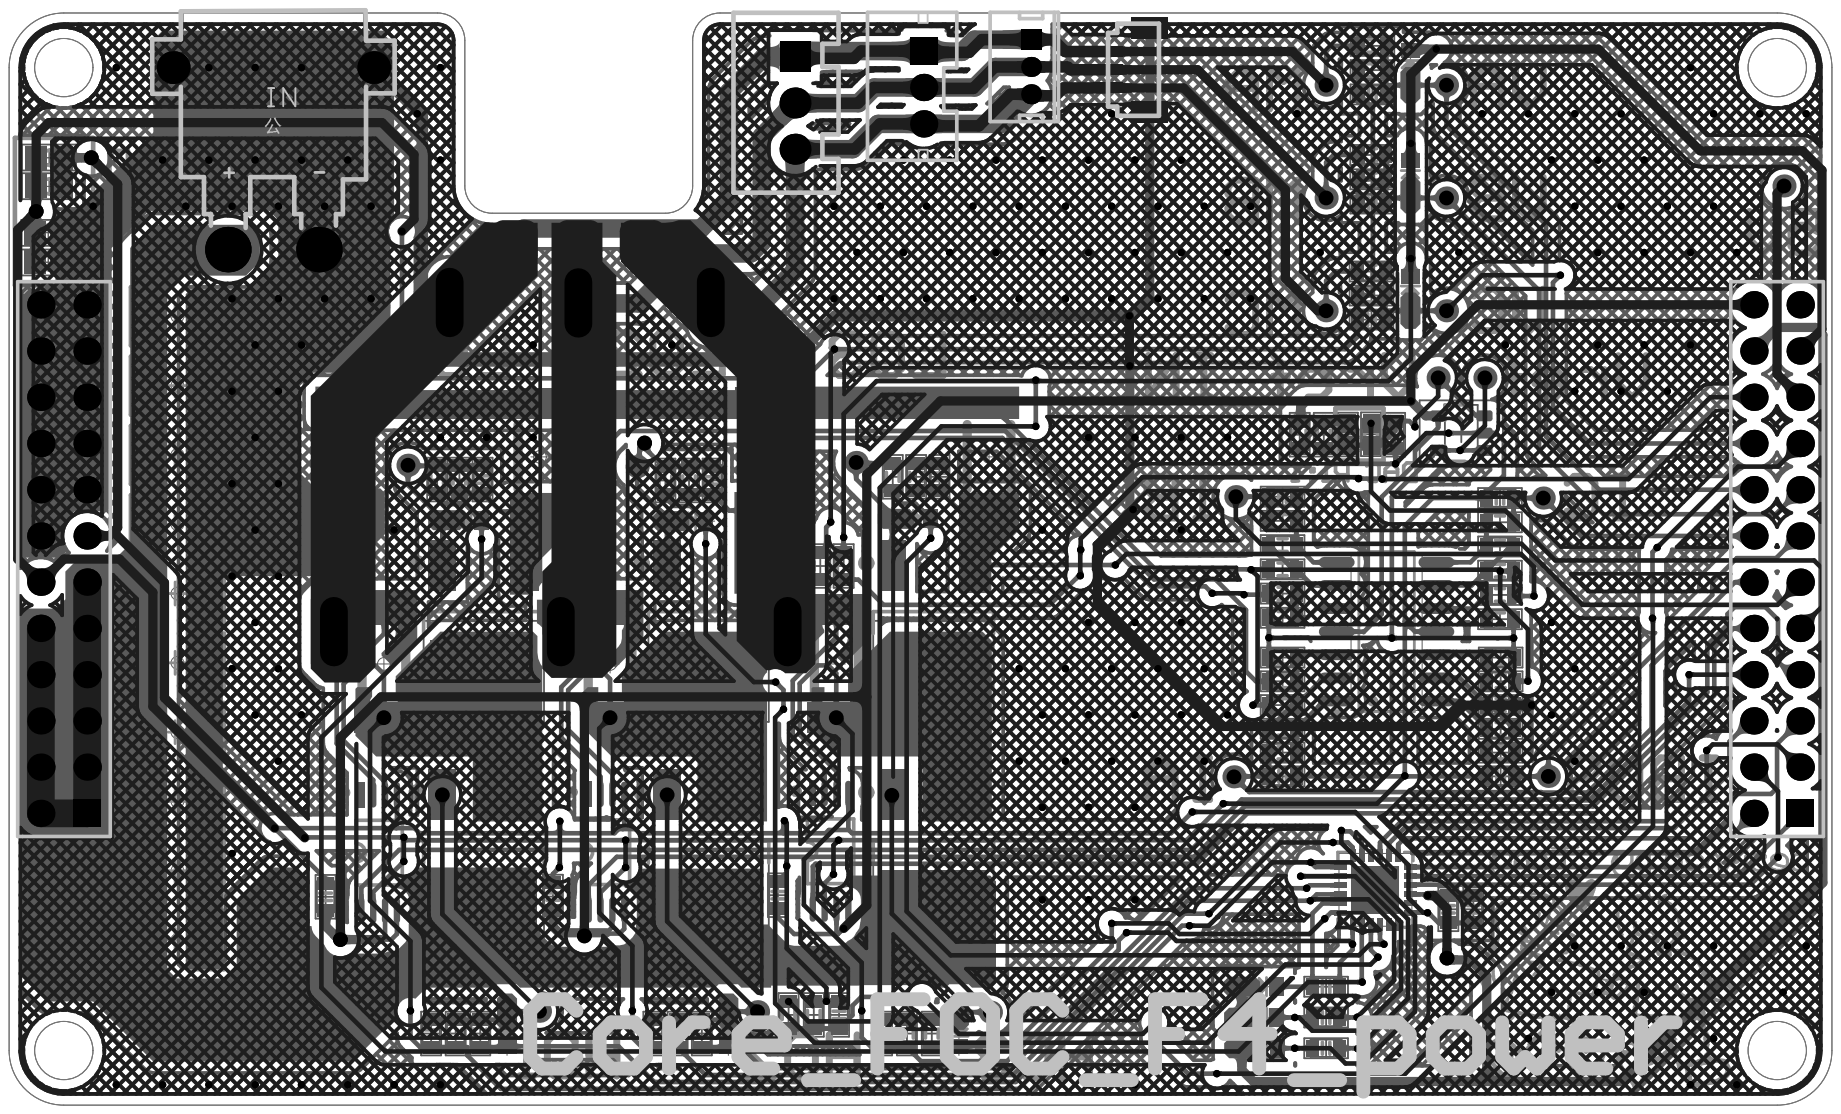
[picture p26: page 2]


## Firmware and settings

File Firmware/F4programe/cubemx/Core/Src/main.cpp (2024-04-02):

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
/* Includes ------------------------------------------------------------------*/
#include "main.h"
#include "adc.h"
#include "can.h"
#include "dma.h"
#include "i2c.h"
#include "spi.h"
#include "tim.h"
#include "usart.h"
#include "usb_otg.h"
#include "gpio.h"

/* USER CODE BEGIN Includes */
#include "usart_cpp/bsp_usart.hpp"
#include "Beep/bsp_beep.h"
#include "timer/timer.hpp"
#include "st7735s/bsp_st7735s.h"
#include "Can/bsp_can.h"
#include "tle5012b/bsp_tle5012b.h"
#include "Key_cpp/bsp_key.hpp"
#include "foc_cpp/bsp_foc.hpp"
#include "app_encoder/app_encoder.hpp"
#include "serialdebug/bsp_serialdebug.hpp"
/* USER CODE END Includes */


void SystemClock_Config(void);
/**
 * @brief  The application entry point.
 * @retval int
 */
int main(void)
{
  /* MCU Configuration--------------------------------------------------------*/

  /* Reset of all peripherals, Initializes the Flash interface and the Systick. */
  HAL_Init();

  /* Configure the system clock */
  SystemClock_Config();

  /* Initialize all configured peripherals */
  MX_GPIO_Init();
  MX_DMA_Init();
  MX_TIM1_Init();
  MX_ADC1_Init();
  MX_CAN1_Init();
  MX_I2C2_Init();
  MX_SPI1_Init();
  MX_SPI3_Init();
  MX_TIM2_Init();
  MX_TIM3_Init();
  MX_TIM5_Init();
  MX_TIM8_Init();
  MX_TIM14_Init();
  MX_USART1_UART_Init();
  MX_USB_OTG_FS_PCD_Init();
  MX_TIM4_Init();
  MX_ADC2_Init();
  /* USER CODE BEGIN 2 */

  /* 按键初始化 */
  Button_L.clean();
  Button_M.clean();
  Button_R.clean();

  /* 电机初始化 */
  motor.set_encoder(&HallEncoder);
  motor.encoder_dir = REVERSE;
  motor.set_PID_IQ(&motor_pid_IQ);
  motor.set_PID_ID(&motor_pid_ID);
  motor.set_PID_IN(&motor_pid_in);
  motor.set_PID_OUT(&motor_pid_out);
  motor.set_voltage_limit(12, 13);
  motor.set_ZeroElectricalAngle(0.874368f); // 三孔小电机
  // motor.set_ZeroElectricalAngle(2.365873f);
  motor.init();

  /* motor 电流采样初始化 */
  motor.set_current_sensor(&foc_current_sensor);
  motor._current_sensor->init(0, 1, 2);
  //  motor._current_sensor->init(3, 4, 5);
  motor._current_sensor->calibration(100);

  /* 串口初始化 */
  USART_Debug_DMA_Init();

  /* CAN 初始化 */
  bsp_can_Init();

  /* st7735s 显示屏初始化 */
  bsp_st7735s_init(R0);

  /* 播放启动音乐 */
  // bsp_beep_Music_Play(warning);

  /* 默认电机上电 */
  // motor.enable();
  motor.disable();
  // motor.set_speed(60);
  motor.set_speed(60, openloop);
  // motor.set_current(-0.5);
  // motor.set_speed(180);
  // motor.set_degree(360);

  /* vofa+ 初始化 */
  // serial_test.check_frame_length();

  /* 定时器初始化 */
  timer_init();

  // motor.init_ZeroElectricalAngle(1000);
  // motor.init_ZeroElectricalAngle(1000);
  // motor.init_ZeroElectricalAngle(1000);
  // motor.init_ZeroElectricalAngle(1000);
  // motor.init_ZeroElectricalAngle(1000);
  // motor.init_ZeroElectricalAngle(1000);
  // motor.init_ZeroElectricalAngle(1000);
  // motor.init_ZeroElectricalAngle(1000);

  /* USER CODE END 2 */

  /* Infinite loop */
  /* USER CODE BEGIN WHILE */
  while (1)
  {
    /* USER CODE END WHILE */

    /* USER CODE BEGIN 3 */

    // printf("hello world");

    // bsp_beep_Music_Handle();
    // printf("tle5012b = %f \r\n", ReadAngle());
    // printf("tle5012b = %f \r\n", motor._encoder->date);
    // printf("%5f  %5f  %5f\r\n",motor.Uu, motor.Uv, motor.Uw);
    // printf("Button State: %4d %4d %4d \r\n", Button_L.OUT_State, Button_M.OUT_State, Button_R.OUT_State);
    // printf("%5f  %5f  %5f\r\n",
    //        motor._current_sensor->phase_u.data,
    //        motor._current_sensor->phase_v.data,
    //        motor._current_sensor->phase_w.data);

    serial_test.config_data(motor.target_degree);
    serial_test.config_data(motor.degree);
    serial_test.config_data(motor.target_speed);
    serial_test.config_data(motor.speed);
    // serial_test.config_data(motor.target_current);
    // serial_test.config_data(motor.I_q);
    // serial_test.config_data(motor.U_q);

    serial_test.config_data(motor._current_sensor->phase_u.data);
    serial_test.config_data(motor._current_sensor->phase_v.data);
    serial_test.config_data(motor._current_sensor->phase_w.data);

    //  serial_test.config_data(motor.Svpwm_Mod.ta);
    // serial_test.config_data(motor.Svpwm_Mod.tb);
    // serial_test.config_data(motor.Svpwm_Mod.tc);

    serial_test.send_frame();

    // printf("%5f  %5f\r\n",
    //        motor.I_q,
    //        motor.I_d);

    if (Button_M.OUT_State == Button_ON)
    {
      motor.enable();
    }
    else
    {
      motor.disable();
    }

    HAL_Delay(1);
  }
  /* USER CODE END 3 */
}

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


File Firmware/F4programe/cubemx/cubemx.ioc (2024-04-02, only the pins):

Mcu.UserName=STM32F405RGTx
PA0-WKUP.Signal=S_TIM5_CH1
PA1.Signal=ADCx_IN1
PA10.Signal=S_TIM1_CH3
PA11.Signal=USB_OTG_FS_DM
PA12.Signal=USB_OTG_FS_DP
PA13.Signal=SYS_JTMS-SWDIO
PA14.Signal=SYS_JTCK-SWCLK
PA15.Signal=S_TIM2_CH1_ETR
PA2.Signal=ADCx_IN2
PA3.Signal=ADCx_IN3
PA4.Signal=ADCx_IN4
PA5.Signal=ADCx_IN5
PA6.Signal=ADCx_IN6
PA7.Signal=S_TIM14_CH1
PA8.Signal=S_TIM1_CH1
PA9.Signal=S_TIM1_CH2
PB0.Signal=ADCx_IN8
PB1.Signal=ADCx_IN9
PB10.Signal=I2C2_SCL
PB11.Signal=I2C2_SDA
PB12.GPIO_Label=LCD_DC
PB12.Signal=GPIO_Output
PB13.Signal=TIM1_CH1N
PB14.Signal=TIM1_CH2N
PB15.Signal=TIM1_CH3N
PB2.GPIO_Label=LCD_RES
PB2.Signal=GPIO_Output
PB3.Signal=SPI1_SCK
PB4.Signal=SPI1_MISO
PB5.Signal=SPI1_MOSI
PB6.Signal=USART1_TX
PB7.Signal=USART1_RX
PB8.Signal=CAN1_RX
PB9.Signal=CAN1_TX
PC0.Signal=ADCx_IN10
PC1.Signal=ADCx_IN11
PC10.Signal=SPI3_SCK
PC11.GPIO_Label=SPI3_CS
PC11.Signal=GPIO_Output
PC12.Signal=SPI3_MOSI
PC13-ANTI_TAMP.GPIO_Label=BUTTON_L
PC13-ANTI_TAMP.Signal=GPIO_Input
PC14-OSC32_IN.GPIO_Label=BUTTON_M
PC14-OSC32_IN.Signal=GPIO_Input
PC15-OSC32_OUT.GPIO_Label=BUTTON_R
PC15-OSC32_OUT.Signal=GPIO_Input
PC2.Signal=ADCx_IN12
PC3.Signal=ADCx_IN13
PC4.Signal=ADCx_IN14
PC5.Signal=ADCx_IN15
PC6.Signal=S_TIM3_CH1
PC7.Signal=S_TIM3_CH2
PC8.GPIO_Label=ENCODER_Z
PC8.Signal=GPIO_Input
PC9.Signal=S_TIM8_CH4
PD2.GPIO_Label=SPI1_CS
PD2.Signal=GPIO_Output
PH0-OSC_IN.Signal=RCC_OSC_IN
PH1-OSC_OUT.Signal=RCC_OSC_OUT

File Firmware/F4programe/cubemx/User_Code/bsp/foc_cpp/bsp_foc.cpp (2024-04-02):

/**
 * @file bsp_foc.cpp
 * @brief foc板级支持包
 * @author Tony_Wang
 * @version 2.0 Beta
 * @date 2023-9-18
 * @copyright
 * @par 日志:
 *   V1.0 		基本构建，完成： 1.开环速度控制 2.基于编码器的位置闭环控制
 * 	 V1.1 		重写运行逻辑，改为模式运行
 *	 V2.0 Beta  新增电流采样和电流闭环，但是没有调通
 */

#include "bsp_foc.hpp"
#include "tim.h"

// #include "stm32f4xx_ll_cortex.h"
#include <math.h>

#define WEAK __attribute__((weak)) // 使用WEAK类型是方便特殊电机来重构特定函数

/* 默认声明变量样例 */
pwmio pwm_u(&htim1, TIM_CHANNEL_1, PWM_ENABLE);
pwmio pwm_v(&htim1, TIM_CHANNEL_2, PWM_ENABLE);
pwmio pwm_w(&htim1, TIM_CHANNEL_3, PWM_ENABLE);
// foc motor(&pwm_u, &pwm_v, &pwm_w, 7, REVERSE);
foc motor(&pwm_u, &pwm_v, &pwm_w, 7, FORWARD);
pid motor_pid_out(5.0f, 0.0f, 100.0f, 0.0f, 300.0f);
pid motor_pid_in(0.006f, 0.00002f, 0.0f, 0.5f, 1.8f);

float current_p = -0.5f;
// float current_i = -0.001f;
float current_i = current_p / 10;
// float current_i = -0.0f;
float current_i_max = 5.0f;
float current_pid_max = 5.0f;
pid motor_pid_IQ(current_p, current_i, 0.0f, current_i_max, current_pid_max);
pid motor_pid_ID(current_p, current_i, 0.0f, current_i_max, current_pid_max);

current_sensor foc_current_sensor = current_sensor(&bsp_adc_dma1);

/* pwmio 构造函数 */
WEAK pwmio::pwmio(TIM_HandleTypeDef *htim, uint32_t TIM_CHANNEL, PWM_STATE __TIM_EX_FLAG)
{
	this->htim = htim;
	this->TIM_CHANNEL = TIM_CHANNEL;
	this->ccr = 0;

	this->__TIM_EX_FLAG = __TIM_EX_FLAG;
}

/**
 * @brief  设置 pwmio 的 比较值
 * @details
 * @param  ccr :比较值
 * @retval
 */
void pwmio::set_ccr(uint16_t ccr)
{
	this->ccr = ccr;
	__HAL_TIM_SET_COMPARE(this->htim, this->TIM_CHANNEL, this->ccr);
}

/**
 * @brief  开启 pwm 输出
 * @details
 * @param  state :enable disable
 * @retval
 */
void pwmio::set_state(PWM_STATE state)
{
	this->state = state;
	if (state == PWM_ENABLE)
	{
		if (this->__TIM_EX_FLAG == PWM_ENABLE)
		{
			HAL_TIMEx_PWMN_Start(this->htim, TIM_CHANNEL);
		}
		HAL_TIM_PWM_Start(this->htim, TIM_CHANNEL);
	}
	else if (state == PWM_DISABLE)
	{
		if (this->__TIM_EX_FLAG == PWM_ENABLE)
		{
			HAL_TIMEx_PWMN_Stop(this->htim, TIM_CHANNEL);
		}
		HAL_TIM_PWM_Stop(this->htim, this->TIM_CHANNEL);
	}
}

////******************************************* foc 电机类*************************************************************************////
/**
	* @brief  foc 电机类
	* @param [in]   *pwm_u			U 通道 pwm
	* @param [in]	*pwm_v			V 通道 pwm
	* @param [in]	*pwm_w			W 通道 pwm
	* @param [in]	*EN_GPIO_Port	电机使能端口号
	* @param [in]	EN_GPIO_Pin		电机使能引脚号
	* @param [in]	pole_pairs		电机极对数

	*
*/

WEAK foc::foc(pwmio *pwm_u, pwmio *pwm_v, pwmio *pwm_w, int pole_pairs, DIR_STATE dir, GPIO_TypeDef *EN_GPIO_Port, uint16_t EN_GPIO_Pin)
{
	this->pwm_u = pwm_u;
	this->pwm_v = pwm_v;
	this->pwm_w = pwm_w;
	this->pole_pairs = pole_pairs;
	this->dir = dir;

	/* 电机使能IO配置 */
	this->EN_GPIO_Port = EN_GPIO_Port;
	this->EN_GPIO_Pin = EN_GPIO_Pin;

	// 全幅限制，保护电机不转
	this->voltage_limit = 0;
	this->voltage_power_supply = 5;
}

/**
 * @brief  foc 初始化函数
 * @details	包括开启使用的三个pwm定时器，读取定时器的 重装载值
 * @param
 * @retval
 */
void foc::init(void)
{
	// this->pwm_u->set_state(PWM_ENABLE);
	// this->pwm_v->set_state(PWM_ENABLE);
	// this->pwm_w->set_state(PWM_ENABLE);

	this->pwm_u->set_ccr(0);
	this->pwm_v->set_ccr(0);
	this->pwm_w->set_ccr(0);
	_tim_autoreload = __HAL_TIM_GetAutoreload(this->pwm_u->htim);

	/* 给一个50%的占空比，让adc校准有下降沿触发 */
	this->run_UVW(0.5 * this->voltage_power_supply, 0.5 * this->voltage_power_supply, 0.5 * this->voltage_power_supply);
}

/**
 * @brief  foc 上电
 * @details	使能foc
 * @param
 * @retval
 */
void foc::enable(void)
{
	if (this->motor_state != FOC_ENABLE)
	{
		if (this->EN_GPIO_Port != nullptr)
		{
			HAL_GPIO_WritePin(this->EN_GPIO_Port, this->EN_GPIO_Pin, GPIO_PIN_SET);
		}
		this->pwm_u->set_state(PWM_ENABLE);
		this->pwm_v->set_state(PWM_ENABLE);
		this->pwm_w->set_state(PWM_ENABLE);
		motor_state = FOC_ENABLE;
	}
}

/**
 * @brief  foc 下电
 * @details	使能foc
 * @param
 * @retval
 */
void foc::disable(void)
{
	if (this->motor_state != FOC_DISABLE)
	{
		if (this->EN_GPIO_Port != nullptr)
		{
			HAL_GPIO_WritePin(this->EN_GPIO_Port, this->EN_GPIO_Pin, GPIO_PIN_RESET);
		}
		this->pwm_u->set_state(PWM_DISABLE);
		this->pwm_v->set_state(PWM_DISABLE);
		this->pwm_w->set_state(PWM_DISABLE);
		motor_state = FOC_DISABLE;
		__HAL_TIM_ENABLE(&htim1); // ！！关闭PWM输出会自动失能定时器，需要手动打开
	}
}

/**
 * @brief  foc 输出限制配置函数
 * @details
 * @param  	voltage_limit :限制的输出电压
 * @param  	voltage_power_supply :提供的电源电压
 * @retval
 */
void foc::set_voltage_limit(float voltage_limit, float voltage_power_supply)
{
	this->voltage_limit = _constrain(voltage_limit, 0.0f, voltage_power_supply);
	this->voltage_power_supply = voltage_power_supply;
}

/**
 * @brief  foc 编码器设置函数
 * @details
 * @param  	_encoder :链接配置的编码器，这是一个软核，输出要求为弧度值[0,2PI]
 * @retval
 */
void foc::set_encoder(encoder *_encoder)
{
	this->_encoder = _encoder;
}

/**
 * @brief  foc 编码器设置滤波器函数
 * @details	定义里面 new 了一个 LowPassFilter 类，调用设定函数的 delete 默认的
 * @param  	_encoder :链接配置的编码器，这是一个软核，输出要求为弧度值[0,2PI]
 * @retval
 */
void foc::set_SPEED_LowPassFilter(LowPassFilter *_SPEED_LowPassFilter)
{
	delete this->_SPEED_LowPassFilter; // 释放默认的滤波器
	this->_SPEED_LowPassFilter = _SPEED_LowPassFilter;
}

/**
 * @brief  foc q电流环设置滤波器函数
 * @details	定义里面 new 了一个 LowPassFilter 类，调用设定函数的 delete 默认的
 * @param  	_encoder :链接配置的编码器，这是一个软核，输出要求为弧度值[0,2PI]
 * @retval
 */
void foc::set_Iq_LowPassFilter(LowPassFilter *_Iq_LowPassFilter)
{
	delete this->_Iq_LowPassFilter; // 释放默认的滤波器
	this->_Iq_LowPassFilter = _Iq_LowPassFilter;
}

/**
 * @brief  foc d电流环设置滤波器函数
 * @details	定义里面 new 了一个 LowPassFilter 类，调用设定函数的 delete 默认的
 * @param  	_encoder :链接配置的编码器，这是一个软核，输出要求为弧度值[0,2PI]
 * @retval
 */
void foc::set_Id_LowPassFilter(LowPassFilter *_Id_LowPassFilter)
{
	delete this->_Id_LowPassFilter; // 释放默认的滤波器
	this->_Id_LowPassFilter = _Id_LowPassFilter;
}

/**
 * @brief  foc 外环设置函数
 * @details
 * @param  	_PID_OUT :链接配置的 pid 类，用于控制位置闭环的，属于外环
 * @retval
 */
void foc::set_PID_OUT(pid *_PID_OUT)
{
	this->_PID_OUT = _PID_OUT;
}

/**
 * @brief  foc 内环设置函数
 * @details
 * @param  	_PID_IN :链接配置的 pid 类，用于控制速度闭环的，属于内环
 * @retval
 */
void foc::set_PID_IN(pid *_PID_IN)
{
	this->_PID_IN = _PID_IN;
}

/**
 * @brief  foc 输出函数
 * @details 默认以中间计算的三相占空比输出
 * @param
 * @retval
 */
void foc::run_UVW(void)
{
	/* 跳转至带输入参数的 */
	this->run_UVW(this->Uu, this->Uv, this->Uw);
}

/**
 * @brief  foc 输出函数
 * @details
 * @param  	Uu :u相输出电压
 * @param  	Uv :v相输出电压
 * @param  	Uw :w相输出电压
 * @retval
 */
void foc::run_UVW(float Uu_in, float Uv_in, float Uw_in)
{
	// 设置上限
	Uu_in = _constrain(Uu_in, 0.6f, voltage_limit);
	Uv_in = _constrain(Uv_in, 0.6f, voltage_limit);
	Uw_in = _constrain(Uw_in, 0.6f, voltage_limit);
	this->Uu = Uu_in;
	this->Uv = Uv_in;
	this->Uw = Uw_in;

	// 计算占空比，写入到pwm
	this->pwm_u->set_ccr(Uu / voltage_power_supply * _tim_autoreload);
	this->pwm_v->set_ccr(Uv / voltage_power_supply * _tim_autoreload);
	this->pwm_w->set_ccr(Uw / voltage_power_supply * _tim_autoreload);
}
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

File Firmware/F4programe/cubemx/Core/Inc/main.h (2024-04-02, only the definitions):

#define BUTTON_L_Pin GPIO_PIN_13
#define BUTTON_L_GPIO_Port GPIOC
#define BUTTON_M_Pin GPIO_PIN_14
#define BUTTON_M_GPIO_Port GPIOC
#define BUTTON_R_Pin GPIO_PIN_15
#define BUTTON_R_GPIO_Port GPIOC
#define LCD_RES_Pin GPIO_PIN_2
#define LCD_RES_GPIO_Port GPIOB
#define LCD_DC_Pin GPIO_PIN_12
#define LCD_DC_GPIO_Port GPIOB
#define ENCODER_Z_Pin GPIO_PIN_8
#define ENCODER_Z_GPIO_Port GPIOC
#define SPI3_CS_Pin GPIO_PIN_11
#define SPI3_CS_GPIO_Port GPIOC
#define SPI1_CS_Pin GPIO_PIN_2
#define SPI1_CS_GPIO_Port GPIOD

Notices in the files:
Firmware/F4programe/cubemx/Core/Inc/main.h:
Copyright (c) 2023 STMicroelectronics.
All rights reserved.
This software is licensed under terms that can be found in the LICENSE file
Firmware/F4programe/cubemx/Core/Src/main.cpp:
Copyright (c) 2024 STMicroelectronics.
